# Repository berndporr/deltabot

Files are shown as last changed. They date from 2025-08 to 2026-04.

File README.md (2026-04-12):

# The Delta Bot

## What is the Delta Bot?
The Delta Bot is an open-source DIY robot AI platform that uses Radxa's single board computer, 

 - the [Rock 5B+](https://radxa.com/products/rock5/5b/),
 - Parallax's [Continuous Rotation Servo Motors](https://www.parallax.com/product/parallax-continuous-rotation-servo-factory-centered/),
 - C1 LIDAR https://github.com/berndporr/c1lidar and
 - Raspberry PI V2 camera

<p align="center">
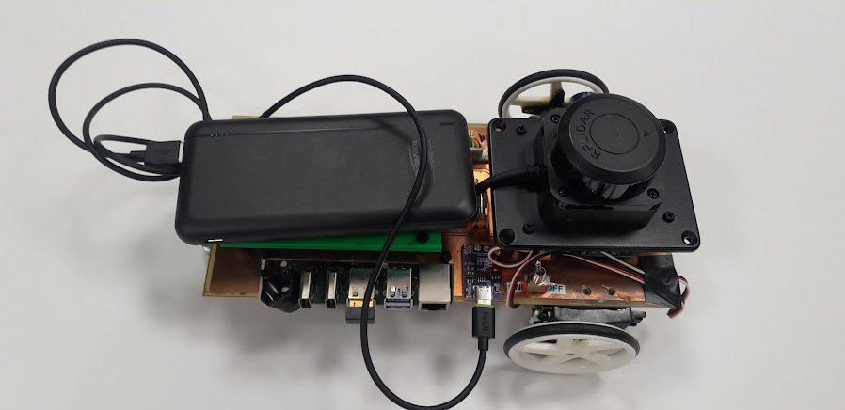
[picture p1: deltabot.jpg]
  
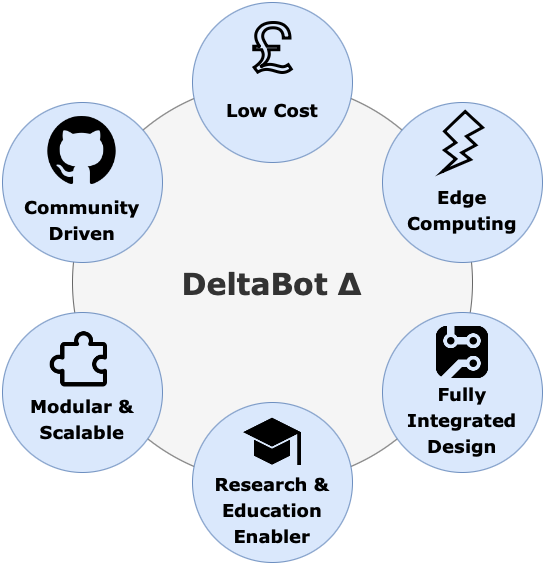
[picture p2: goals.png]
  
</p>

## Hardware

### Schematics
For details on the DeltaBot schematic, pcb, and footprint library refer to the subfolder [schematic_files](schematic_files).

### Connectors

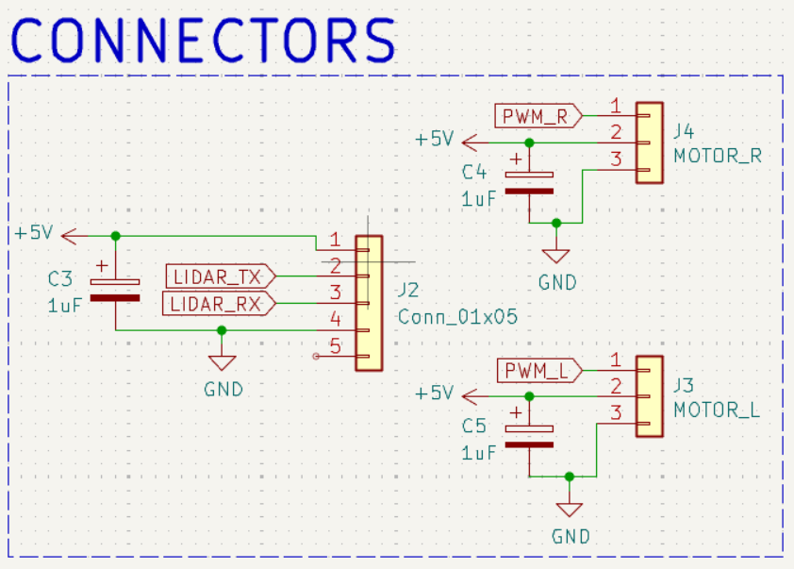
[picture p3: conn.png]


Plug the right motor into J4, the left motor into J3 and the LIDAR into J2.

### Additional Mechanical Parts
Additional Mechanical Parts were designed in CAD and can be accessed [here](additional_files/deltabot.f3z):
<p align="center">
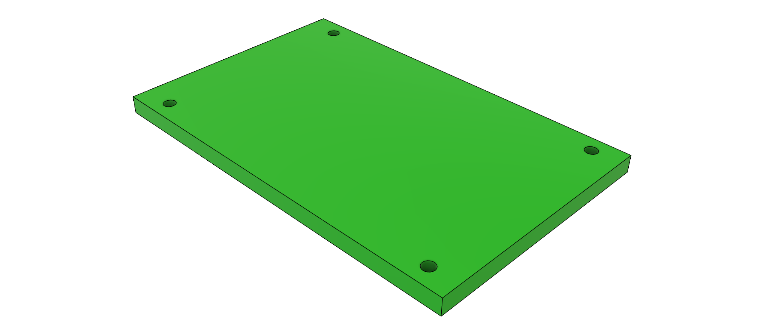
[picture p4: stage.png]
Front View
  
</p>
In particular the "stage" which holds the power bank.

## Software

### Install ARMbian

Download from
https://www.armbian.com/rock-5b/
the image "Armbian 25.8.2 Bookworm Minimal / IOT".
the 
Call `armbian-config`:
  - upgrade to Debian "trixie"
  - Make sure you have kernel 26.2.1 Armbian Linux vendor headers 6.1.115-vendor-rk35xx

### PWM motor drivers

Start `sudo nano /boot/armbianEnv.txt`, identify these lines and add/edit them that
they look like these:

```
console=display
overlay_prefix=
overlays=rk3588-pwm14-m0 rk3588-pwm8-m0
```

This enables the UART and PWM on the pins 33 and 34 on the 40 pin header.

Create the group `gpio`:

```
groupadd gpio
```
and add yourself and other users to it who want to write to the PWM device.

Copy the file [90-gpio.rules](90-gpio.rules) to `/etc/udev/rules.d/`. This will
make sure that the PWM can accessed by any user who's in the gpio group.

The library and example programs how to control the motors are in [wheeleddrive](wheeleddrive).

### LIDAR

Enable the UART for serial communication. Start `sudo nano /boot/armbianEnv.txt`, identify these lines and add `rk3588-uart2-m0` to overlays.

```
overlay_prefix=
overlays=rk3588-uart2-m0
```

Add yourself to the group `dialout` to access /dev/tty*.

The driver and example programs are here: https://github.com/berndporr/c1lidar

### Raspberry PI V2 Cameras

The 1st RPI V2 camera has already a device overlay (`rock-5b-rpi-camera-v2`). The device overlay for the 2nd camera
needs to be compiled from source:

```
cpp -nostdinc -I /usr/src/linux-headers-6.1.115-vendor-rk35xx/include/ -undef -x assembler-with-cpp rock-5b-plus-cam1-rpi-camera-v2.dts > cam1.dts
dtc -@ -I dts -O dtb -o /tmp/rock-5b-plus-cam1-rpi-camera-v2.dtbo cam1.dts
cp /tmp/rock-5b-plus-cam1-rpi-camera-v2.dtbo /boot/dtb-6.1.115-vendor-rk35xx/rockchip/overlay/
```

Add this to the overlays in `armbianEnv.tex`:
```
overlays=rk3588-pwm14-m0 rk3588-pwm8-m0 rk3588-uart2-m0 rock-5b-rpi-camera-v2 rock-5b-plus-cam1-rpi-camera-v2
```

and reboot.

If all goes well both cameras will show up as:

```
media-ctl -p -d 0

rkcif (platform:rkcif-mipi-lvds2):
	/dev/video0
	/dev/video1
...
	/dev/media0

rkcif (platform:rkcif-mipi-lvds4):
	/dev/video11
	/dev/video12
...
	/dev/video21
	/dev/media1
```

which are the raw devices outputting Bayer patterns. The media device 1 is for the 2nd camera raw processing chain.

The media devices 2 and 3 are the Image Signal Processing chains which decode the images into YUV or Grey images.

To config the cameras you need to config V4L subdevices:

```
v4l2-ctl --device=/dev/v4l-subdev2 -L
v4l2-ctl --device=/dev/v4l-subdev7 -L

User Controls

                       exposure 0x00980911 (int)    : min=0 max=4095 step=1 default=1575 value=1575
                           gain 0x00980913 (int)    : min=256 max=43663 step=1 default=256 value=21960
                horizontal_flip 0x00980914 (bool)   : default=0 value=1
                  vertical_flip 0x00980915 (bool)   : default=0 value=1
```

[See the demo dual camera viewer](opencv-camera-callback) how it's all done in C++!

## Credits
- Saleh AlMulla - 2721704A@student.gla.ac.uk
- Bernd Porr -  bernd.porr@glasgow.ac.uk
- Yixuan Zha - 2974642Z@student.gla.ac.uk

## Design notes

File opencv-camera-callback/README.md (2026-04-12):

# Dual camera viewer

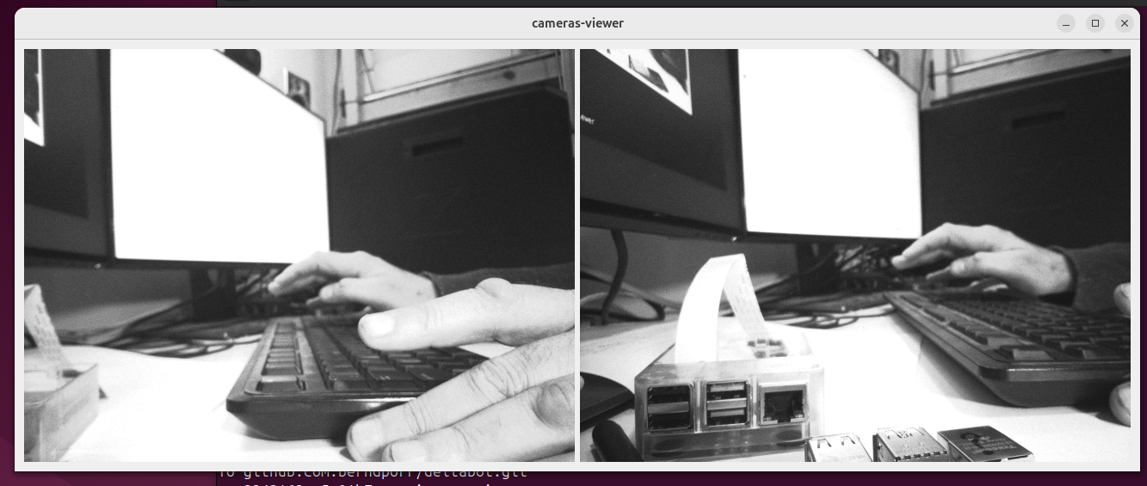
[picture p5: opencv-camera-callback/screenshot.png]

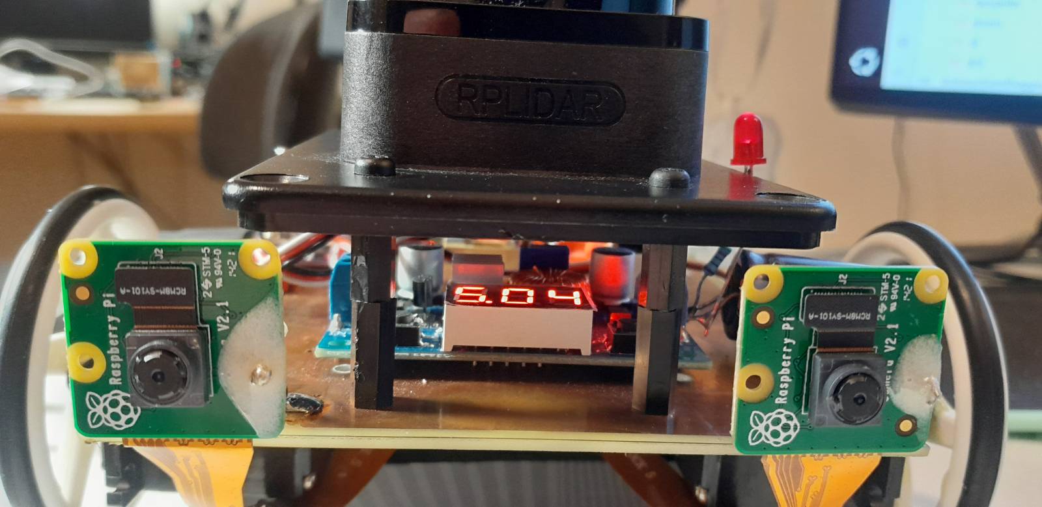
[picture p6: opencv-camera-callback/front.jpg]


## Required packages

```
sudo apt install libopencv-dev
sudo apt-get install qt6-base-dev
```

## Demo program

```
cmake .
make
./cameras-viewer
```

Note that the only FourCC image formats which work on the Rock5 are GREY and NV12 for
B&W and colour respectively.

## Further reading

See https://github.com/berndporr/opencv-camera-callback for in depth discussion about
V4L and its media pipelines.

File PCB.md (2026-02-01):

# DeltaBot PCB Overview

The DeltaBot PCB was designed in **KiCad** with a double-sided layer layout. The design integrates key subsystems including the **Radxa ROCK 5B**, LiDAR sensor, camera module, and servo motors.

<p align="center">
  
</p>

---

## Power System
- Powered via **USB-C Power Delivery (PD)** module at **9V**, stepped down to **5V** using a **DC-DC buck converter**
- A **3.15A fuse** protects against overcurrent
- An **SPDT switch** provides manual ON/OFF control
- A **2200 µF capacitor** suppresses 5V rail ripple for improved voltage stability
- **1 uF** blocking capacitors between each POWER & GND

---

## PCB Layout (Front & Back Layers)

<p align="center">
  
</p>
<p align="center">
  
</p>

---

## ROCK 5B GPIO Pin Assignments

| Function | GPIO Pin(s) | Description |
|---|---|---|
| +5V Power | 2, 4 | Supplies power to board |
| GND | Multiple | Ground reference |
| UART_TX | 8 | TX to LiDAR's RX |
| UART_RX | 10 | RX from LiDAR's TX |
| NC | 18 | NC |
| PWM_L | 32 | PWM control for left servo |
| PWM_R | 33 | PWM control for right servo |

To change or add to the layout, check [here](https://wiki.radxa.com/Rock5/hardware/5b/gpio) for the rock's gpio connections.

---

## Connectors

- **J2 (LiDAR)**: 7-pin Molex
  - UART (TX/RX), 5V & 8.34V power lines
- **J3 / J4 (Servo Motors)**: 3-pin headers  
  - 5V, GND, PWM (Left/Right)

---

## Files

- [Full Schematic](schematic_files/DeltaBot.kicad_sch)
- [PCB Design](schematic_files/DeltaBot.kicad_pcb)
- [PCB Footprints](schematic_files/deltabot.pretty.zip)
- [Rock 5B KiCAD Symbol](schematic_files/deltabot.lib.kicad_sym)
  
---

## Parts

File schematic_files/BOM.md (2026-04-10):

### BOM

- RADXA ROCK5B+
- [SLAMTECH RPLIDAR C1](https://www.slamtec.com/en/c1)
- USB C PD - D/QC/AFC Type-C Fast Charge Trigger Polling Detector PD2.0 PD3.0 To DC Fast Charge Trigger Board Voltage Output
- DC-DC BUCK CONVERTER - DollaTek Small DC Buck Voltage Converter Step Down Voltage Regulator Module Board 4-38V to 1.25-36V 5V/12V Adjustable Output Voltage
- M.2 NVME 256GB - Silicon Power PCIe M.2 NVMe SSD 256GB Gen3x4 R/W up to 2, 100/1, 200MB/s Internal SSD
- x2 Parallax Continuous Rotation Servo Motors - [900-00008 PARALLAX, SERVO- CONTINUOUS ROTATION-S3 SERVO](https://uk.farnell.com/parallax/900-00008/servo-continuous-rotation-s3-servo/dp/2819351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)
- x2 Kitronic Wheels - [2593-SV KITRONIK, Wheel Kit, White, 5 Spoke, ABS, Rotation Servo Motors | Newark Electronics](https://www.newark.com/kitronik/2593-sv/wheels-white-rotation-servo-motor/dp/30AK0833)
- Anker Zolo PowerBank - Anker Zolo Power Bank, 20,000mAh 30W
- 1 x SPDT Toggle Switch
- 1 x F3.15L250V fuse
- 1 x Fuse Holder & 3A Fuse
- 1 x 40 pin 2x20 GPIO Stackable Header 2.54mm
- 2 x 1x3 Pin Header 2.54mm
- 1 x 5 Pin Header 2.54mm - XH2.54-5P 2.54MM straight pin socket

### 3D-Printed:
- Power Bank Stage

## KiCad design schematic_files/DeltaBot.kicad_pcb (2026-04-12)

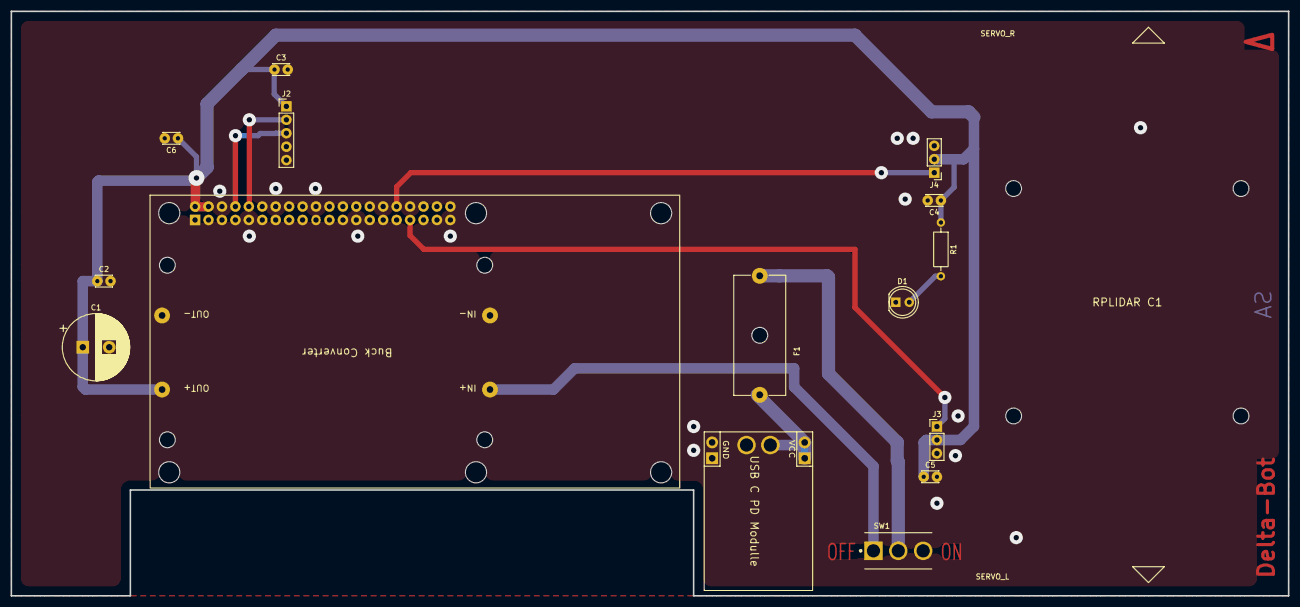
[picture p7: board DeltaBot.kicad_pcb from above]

Board: 2 copper layers, 241.5 x 110.5 mm, 17 parts (1 on the bottom side), 10 nets.

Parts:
C1: 2200uF; CP_Radial_D12.5mm_P5.00mm
C2, C3, C4, C5, C6: 1uF; C_Disc_D3.0mm_W2.0mm_P2.50mm
D1: LED; LED_D5.0mm_Clear
F1: Fuse; Fuseholder_Cylinder-5x20mm_Schurter_0031_8201_Horizontal_Op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
J1: USB C PD Modulle; USB_C
J2: Conn_01x05; PinHeader_1x05_P2.54mm_Vertical
J3: MOTOR_L; PinHeader_1x03_P2.54mm_Vertical
J4: MOTOR_R; PinHeader_1x03_P2.54mm_Vertical
R1: 330R; R_Axial_DIN0207_L6.3mm_D2.5mm_P10.16mm_Horizontal
SW1: SW_SPDT; TE_4-1825136-5
U1: RPLIDAR C1
U1#2: Radxa_ROCK5B; ROCK_5B
U2: Buck Converter; BUCK_CONV

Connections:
+5V: C1.1, C2.1, C3.1, C4.1, C5.1, C6.1, J2.1, J3.2, J4.2, R1.1, U1#2.2 (5V1), U1#2.4 (5V2), U2.3 (OUT+)
+9V: SW1.1 (A), U2.1 (IN+)
GND: C1.2, C2.2, C3.2, C4.2, C5.2, C6.2, D1.1 (K), J1.2 (GND), J1.4 (GND), J2.4, J3.3, J4.3, U1#2.6 (GND1), U1#2.9 (GND8), U1#2.14 (GND2), U1#2.20 (GND3), U1#2.25 (GND7), U1#2.30 (GND4), U1#2.34 (GND5), U1#2.39 (GND6), U2.2 (IN-), U2.4 (OUT-)
LIDAR_RX: J2.3, U1#2.8 (GPIO4_C3)
LIDAR_TX: J2.2, U1#2.10 (GPIO4_C4)
unnamed: D1.2 (A), R1.2
unnamed: F1.2, J1.1 (VCC), J1.3 (VCC)
unnamed: F1.1, SW1.2 (B)
PWM_L: J3.1, U1#2.33 (GPIO2_B4)
PWM_R: J4.1, U1#2.32 (GPIO3_C0)

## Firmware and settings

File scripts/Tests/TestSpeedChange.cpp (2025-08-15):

#include "ServoMotorSetting.h"
#include <thread>
using namespace std;

// This program gradually increases the speed of two servo motors from -10 to 10.
// The speed is changed every second, and the final speed is printed to the console.

int main(int argc, char* argv[])
{
    ServoMotorSetting servo_right(0, 20, 1.52, 14); // 1.5ms
    ServoMotorSetting servo_left(0, 20, 1.52, 8); // 1.5ms

    int speed = -10;

    for(int i = 0; i <= 20; i++)
    {
        servo_left.ChangeLeftSpeed(speed);
        servo_right.ChangeRightSpeed(speed);
        cout << "The speed is: " << speed << endl;
        speed ++;
        std::this_thread::sleep_for(std::chrono::seconds(1));
    }
    servo_left.StopMotor();
    servo_right.StopMotor();

    return 0;
}

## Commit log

2026-02-01 Removed the camera bits
2026-02-01 Added info of how to add the C1 LIDAR.
2026-02-01 Fixed the camera texts.
2026-02-01 Fixed the PCB file
2026-02-01 Removed the Schematic from the front page
2026-04-01 Added camera howto
2026-04-05 Updated PCB layout
    [DeltaBot.kicad_pcb, DeltaBot.kicad_sch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]
2026-04-06 Small changes
    [DeltaBot.kicad_pcb, DeltaBot.kicad_sch]
2026-04-06 Added C1 LIDAR to the footprints.
    [DeltaBot.kicad_pcb]
2026-04-06 Fixed the Rock5B footprint which was slightly off.
    [DeltaBot.kicad_pcb]
2026-04-07 Added files for GU manufacture
    [DeltaBot.kicad_pcb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]
2026-04-07 Updated the PCB according to Andrew's feedback.
    [DeltaBot.kicad_pcb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]
2026-04-07 Updated the gerbers
    [DeltaBot.kicad_pcb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]
2026-04-07 Updated the pads of the 40pin Rock5 header to 2mm pad size.
    [DeltaBot.kicad_pcb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]
2026-04-10 Updated the PCB so that all pads can be soldered without plating through.
    [DeltaBot.kicad_pcb]
2026-04-10 Added an LED to it.
    [DeltaBot.kicad_pcb, DeltaBot.kicad_sch]
2026-04-10 Added more info about the cameras.
2026-04-11 Added framerate request.
2026-04-11 Fixed the USB PD module footprint.
    [DeltaBot.kicad_pcb, DeltaBot.kicad_sch]
2026-04-12 Removed old stuff
    [DeltaBot-B_Cu.gbl, DeltaBot-Edge_Cuts.gm1, DeltaBot-F_Cu.gtl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]
2026-04-12 Added connectors.
2026-04-12 Updated the DollaTek Buck converter.
    [DeltaBot.kicad_pcb]
